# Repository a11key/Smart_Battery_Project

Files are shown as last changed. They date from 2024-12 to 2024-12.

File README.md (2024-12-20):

# Smart_Battery_Project
# Репозиторий проекта "УМНЫЙ АКБ для БАС"

## Министерство науки и высшего образования Российской Федерации  
### ФЕДЕРАЛЬНОЕ ГОСУДАРСТВЕННОЕ АВТОНОМНОЕ ОБРАЗОВАТЕЛЬНОЕ УЧРЕЖДЕНИЕ ВЫСШЕГО ОБРАЗОВАНИЯ  
### «МОСКОВСКИЙ ФИЗИКО-ТЕХНИЧЕСКИЙ ИНСТИТУТ (НАЦИОНАЛЬНЫЙ ИССЛЕДОВАТЕЛЬСКИЙ УНИВЕРСИТЕТ)» (МФТИ, Физтех)

---

## Описание проекта

**Название проекта:** УМНЫЙ АКБ для БАС

**Работу выполнили:**  
- Мацкевич Алексей
- Салахов Камиль 
- Васильев Андрей 

**Дата:** Долгопрудный, 19.12.2024

### Аннотация
Проект направлен на разработку аккумуляторного модуля для беспилотной авиационной системы (БАС), который позволяет передавать параметры АКБ (температуру, напряжение, ток заряда/разряда) на внешнее устройство.

### Цель и задачи
**Цель:** Создать модуль для БАС с возможностью беспроводной связи с внешним устройством для мониторинга параметров аккумуляторов в реальном времени.

**Задачи:**
1. Спроектировать корпус АКБ, позволяющий интегрировать плату для мониторинга параметров и передачи данных на внешнее устройство.
2. Спроектировать плату с датчиками для фиксации состояния АКБ.
3. Разработать программное обеспечение, которое сможет регистрировать данные в режиме реального времени или записывать их в память.

### Использованное оборудование
- 2 платформы Arduino Nano
- 2 высокоточных датчика температуры (±0,25 °C) MCP9808
- LM2596 DC-DC Module (встраиваемый стабилизатор напряжения)
- Датчик Холла ACS712
- 2 радиомодуля NRF24L01 PA LNA
- 3 резистора (10 кОм)

### Ход создания
1. Спроектирована схема основного и принимающего модулей.

2. Попытка распечатать плату под схему. Из-за неудачных попыток создания было принято решение спаять компоненты схемы проводами.

3. Проектирование соединения для соединения АКБ с модулем. Корпус из пластика, распечатанный на 3D-принтере, был бы громоздким и тяжелым, поэтому было принято решение скреплять плату более простым и эффективным способом.

4. Разработано приложение, отображающее параметры, которые были приняты с модуля, прикрепленного к АКБ.

5. Подобраны провода, которые пригодны для использования с аккумулятором Li-Po Fullymax 30C.

### Результаты работы
Создан модуль, позволяющий считывать температуру, напряжение и ток заряда/разряда с АКБ и передавать эти параметры на внешнее устройство.

---

## Установка и использование
В процессе...

---

Для получения дополнительной информации или вопросов, пожалуйста, свяжитесь с авторами проекта.

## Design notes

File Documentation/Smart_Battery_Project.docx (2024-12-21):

Министерство науки и высшего образования Российской Федерации

ФЕДЕРАЛЬНОЕ ГОСУДАРСТВЕННОЕ АВТОНОМНОЕ ОБРАЗОВАТЕЛЬНОЕ УЧРЕЖДЕНИЕ ВЫСШЕГО ОБРАЗОВАНИЯ «МОСКОВСКИЙ ФИЗИКО-ТЕХНИЧЕСКИЙ ИНСТИТУТ (НАЦИОНАЛЬНЫЙ ИССЛЕДОВАТЕЛЬСКИЙ УНИВЕРСИТЕТ)» (МФТИ, Физтех)

ПРОЕКТ

“Умная аккумуляторная батарея для беспилотного авиационного средства”

Работу выполнили: Мацкевич Алексей Б04-305

Салахов Камиль Б04-304

Васильев Андрей Б04-305

Долгопрудный, 2024

# Используемые обозначения

АКБ – аккумуляторная батарея;

БАС – беспилотное авиационное средство;

ПК – персональный компьютер;

ПО – программное обеспечение.

# Аннотация

В данной работе описано создание модуля, подключаемого к БАС (FlameWheel 450), для измерения параметров АКБ (Li-Po Fullymax 30C). Описанный модуль определяет напряжение, ток и температуру АКБ и отправляет эти данные на принимающее устройство (ПК).

Репозиторий с файлами проекта и его описанием: https://github.com/a11key/Smart_Battery_Project.

# Цель и задачи

Цели:

1. Создать модуль для БАС с возможностью беспроводной связи с внешним устройством для мониторинга параметров АКБ (напряжения, температуры, тока заряда/разряда) в реальном времени;
2. Создать ПО для визуализации полученных данных.

Задачи:

- Спроектировать корпус АКБ, позволяющий интегрировать в него плату для мониторинга параметров и передачи данных на внешнее устройство;
- Спроектировать устройство с антенной и датчиками для фиксации состояния АКБ;
- Разработать ПО, сохраняющие данные полученные с устройства, а также строящее графики зависимости фиксируемых величин в реальном времени.

# Требования к проекту

Устройство необходимо изготовить для считывания параметров батареи Li-Po Fullymax 30C (изображена на рисунке 1) при работе квадрокоптера FlameWheel 450 (изображен на рисунке 2).

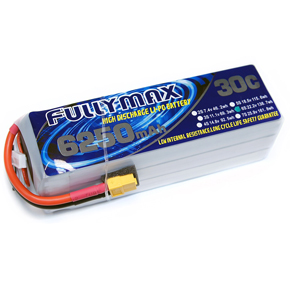
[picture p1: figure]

Рисунок 1 – Аккумулятор Li-Po Fullymax 30C

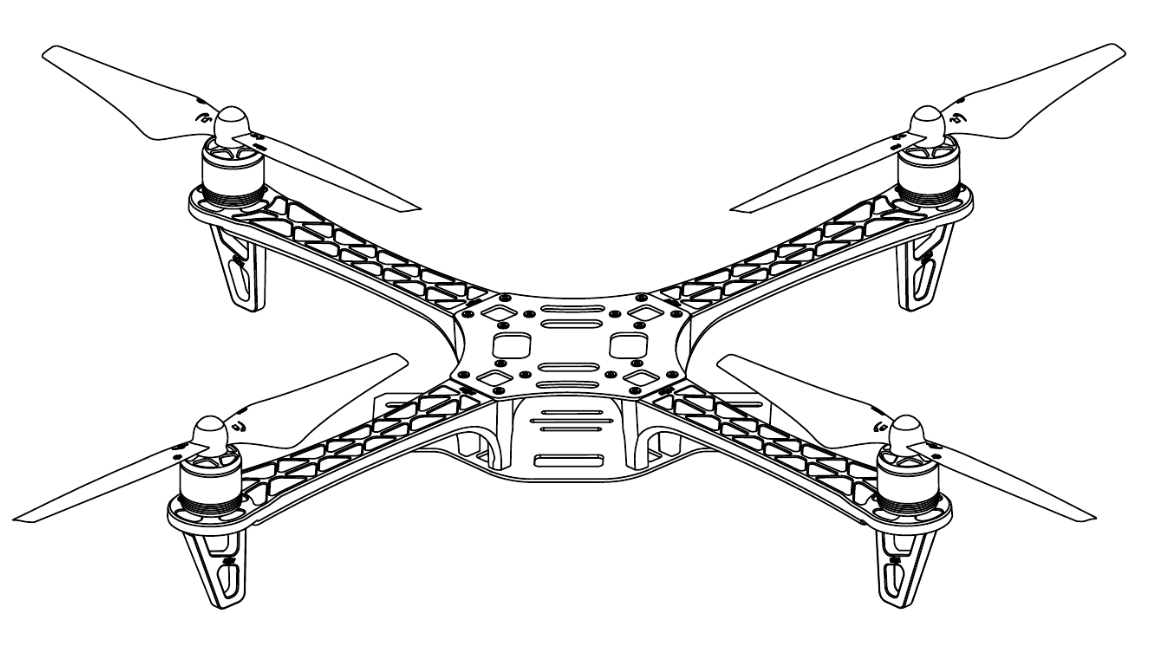
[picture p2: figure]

Рисунок 2 – Квадрокоптер FlameWheel 450

При работе над проектом были сформулированы следующие требования к устройству:

- Дальность действия более 100 м;
- Вес считывающего устройства менее 1/3 веса аккумулятора, то есть менее 130 г.;
- Максимальный потребляемый ток БАС: 30А, следовательно считывающее устройство должно выдерживать токи до 30А.

# Проектирование устройства

Считывающее устройство представляет собой перемычку, подключаемую между батареей и квадрокоптером, имеющую возможность считывать с батареи напряжение, ток и температуру и передавать данные на принимающее устройство.

Пронимающее устройство должно получать данные с считывающего устройства.

Для проектирования обоих устройств за основу был выбран микроконтроллер Arduino Nano.

## Измерение напряжения

Напряжение на аккумуляторе измеряется с помощью простого понижателя напряжения (рисунок 3).

Номиналы резисторов выбирались из следующих соображений:

- Так как аккумулятор получается замкнут на себя через понижающую схему, ток, проходящий через схему понижения, должен быть минимальным, то есть I_(load) ≫I_U . Максимальный ток можно оценить так: 20 А≫I_U . Таким образом суммарное сопротивление должно быть 1,7 Ом≪R_U (Минимальное напряжение аккумулятора ~ 12 В).
- Максимальное напряжение, которое может считать Arduino Nano: 5 В, значит, пониженное напряжение должно не превосходить этого значения.

В итоге были подобраны 3 резистора на 10 кОм. Коэффициент понижения – 3.

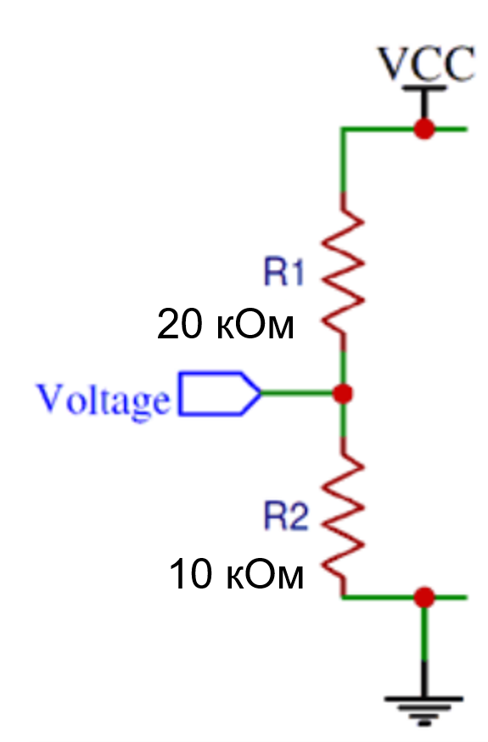
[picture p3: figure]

Рисунок 3 – Схема цепочки для понижения напряжения

## Измерение тока

Изначально планировалось измерять не ток, а напряжение на известном шунтирующем резисторе, а потом преобразовывать его с помощью операционного усилителя, как показано на рисунке 4. Но при подборе шунтирующего резистора оказалось, что резисторы имеющие достаточно маленькое сопротивление (менее 0,17 Ом) и выдерживают достаточно высокую мощность (порядка 300 Вт) имеют стоимость сопоставимую со стоимостью всех остальных компонентов устройства.

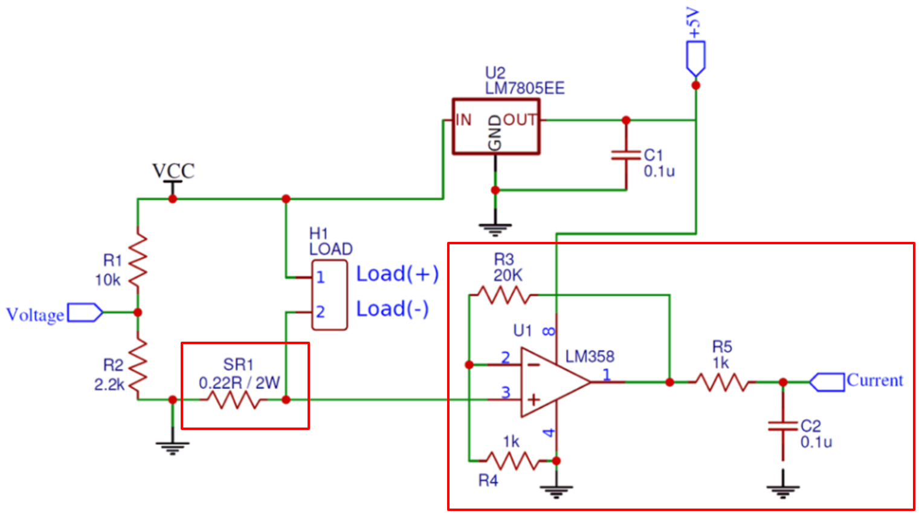
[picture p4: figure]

Рисунок 4 – Схема цепочки для понижения напряжения (часть схемы, используемая для определения силы тока, выделена красным)

Поэтому был выбран альтернативный вариант измерения тока: с помощью датчика ACS712 30A. Датчик рассчитан на максимальный пропускаемый ток 30А, что идеально подходит под требования, создаваемого устройства. Датчик ACS712 изображен на рисунке 5.

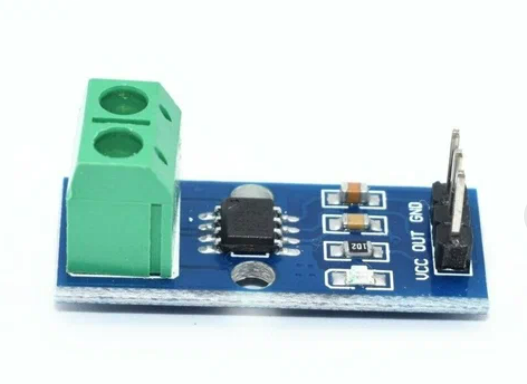
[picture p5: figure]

Рисунок 5 – Датчик тока ACS712 30A

## Измерение температуры

Для измерения температуры были выбраны высокоточные датчики MCP9808. Высокая точность датчиков температуры важна, так как при работе аккумулятора его температура повышается незначительно, однако определение зависимости различных других величин от температуры является ключевой задачей данного проекта. Датчик MCP9808 изображен на рисунке 6.

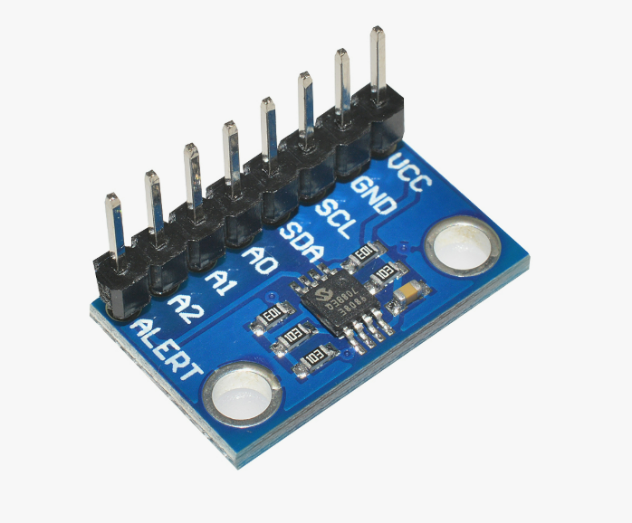
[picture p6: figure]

Рисунок 6 – Высокоточный датчик температуры MCP9808

В измеряющем устройстве было использовано 2 датчика температуры для усреднения температуры. Необходимость этого связана с неравномерностью нагрева АКБ.

## Передача и прием данных

Для передачи и приема данных были использованы радиомодули NRF24L01+PA+LNA, подключенные через специальный адаптер питания к микроконтроллеру. Внешний вид радиомодуля приведен на рисунке 7. Максимальное заявленное расстояние передачи данных – 1 км, что удовлетворяет требованиям к проекту.

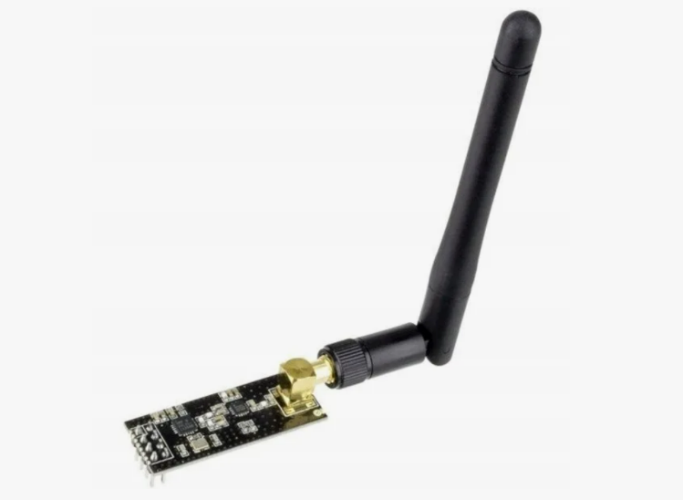
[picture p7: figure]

Рисунок 7 – Радиомодуль NRF24L01+PA+LNA

## Питание устройства

Измеряющее устройство питается с того же аккумулятора, характеристики которого она фиксирует. Питание происходит через стабилизатор LM2596 DC-DC Module, понижающий напряжение до 5 В. Стабилизатор LM2596 DC-DC Module изображен на рисунке 8.

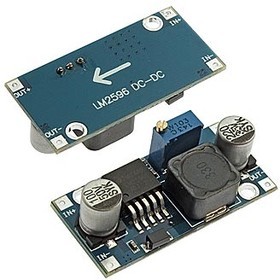
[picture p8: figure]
Фото 1/3 LM2596 DC-DC Module, Встраиваемый стабилизатор напряжения, Uвх=4-40VDC, Uвых=1.5-35VDC

Рисунок 8 – Стабилизатор LM2596 DC-DC Module

## Общая схема устройства

Общая схема измеряющего устройства приведена на рисунке 9.

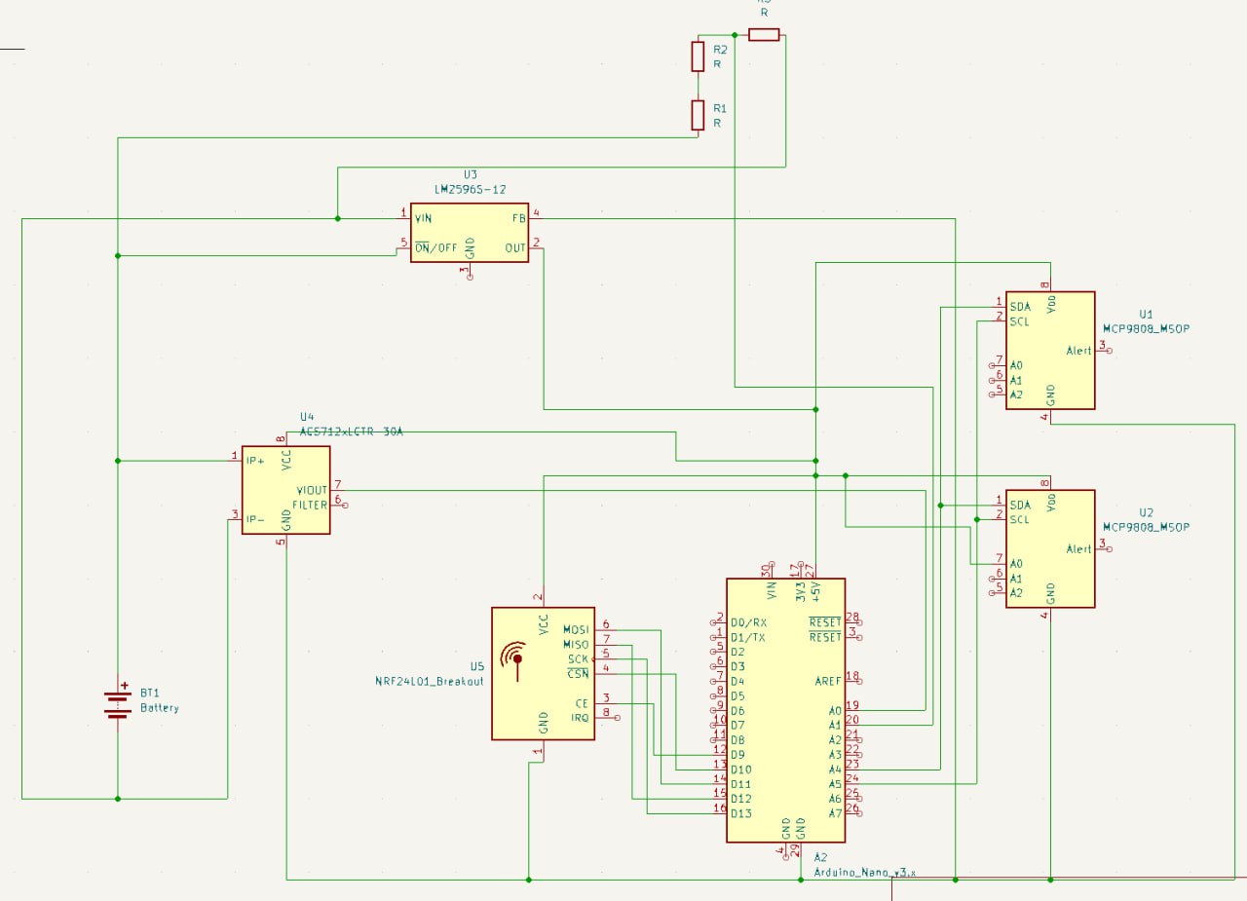
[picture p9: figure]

Рисунок 9 – Схема измеряющего устройства

Схема принимающего устройства изображена на рисунке 10.

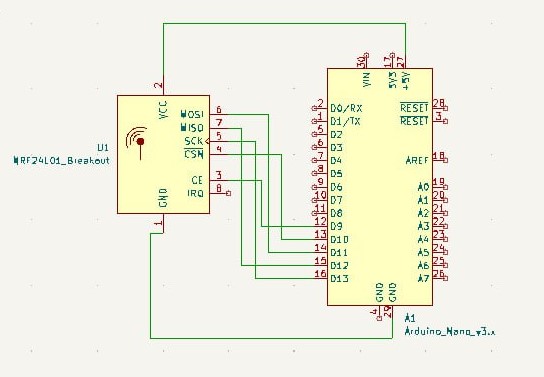
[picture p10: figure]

Рисунок 10 – Принимающего устройства

Изначально планировалось изготовить платы для обеих схем на фрезерно-гравировочном станке Charly 4U (изображен на рисунке 11). Однако после двух неудачных попыток изготовления было решено собирать устройства на макетной плате.

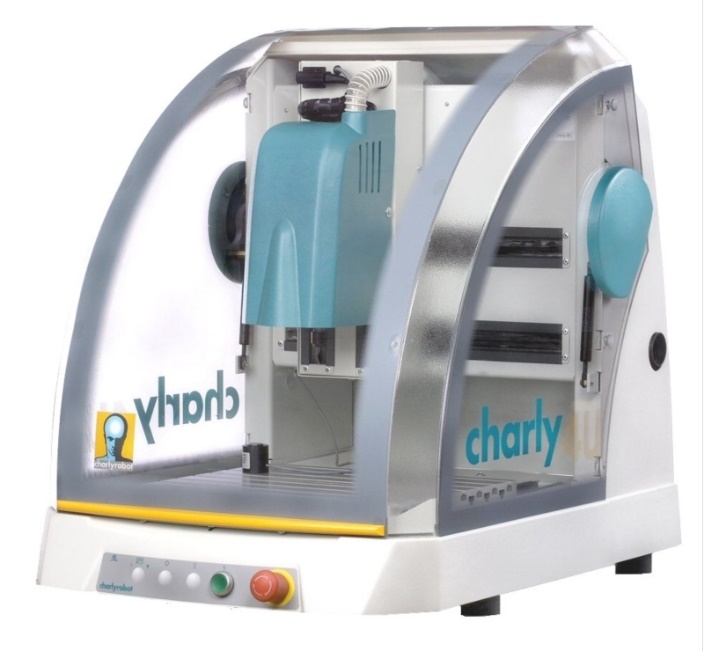
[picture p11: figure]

Рисунок 11 – Фрезерно-гравировочный станок Charly 4U

Разведенная плата принимающего устройства, которую пытались изготовить изображена на рисунке 12.

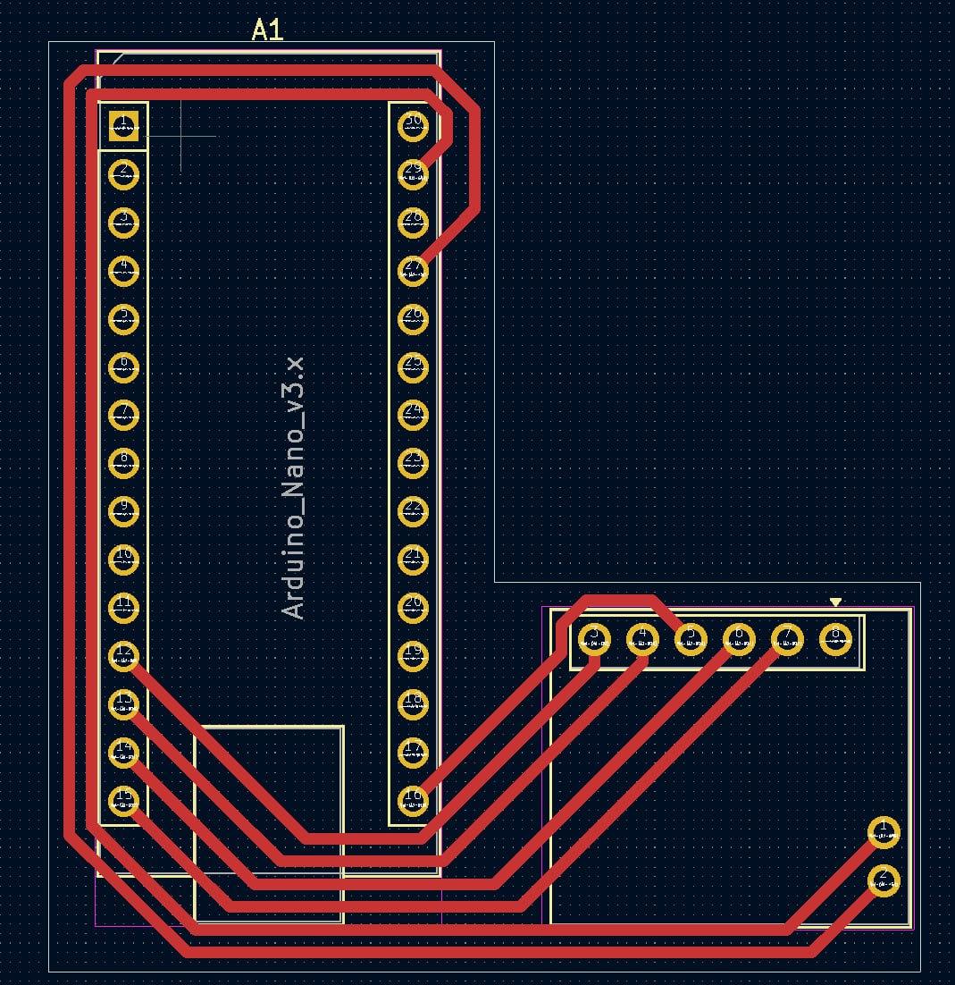
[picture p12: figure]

Рисунок 12 – Схема принимающего устройства

Фото изготовленных устройств представлено на рисунке 13.

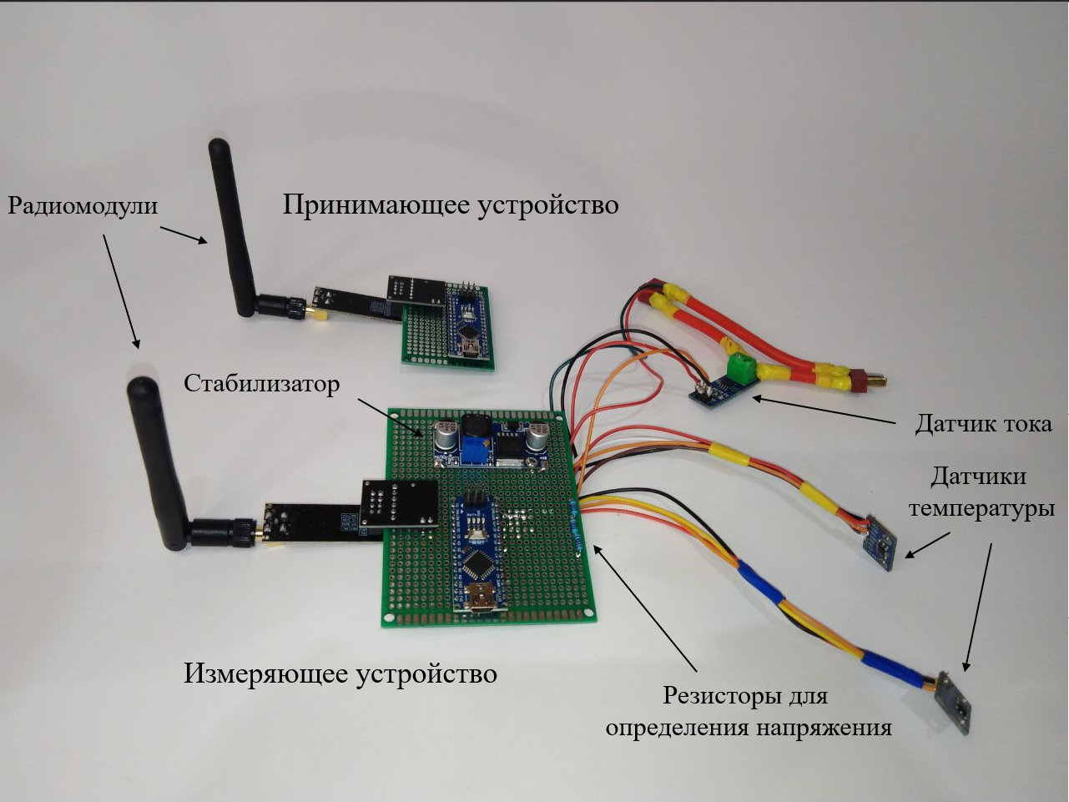
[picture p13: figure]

Рисунок 13 – Готовые измеряющее и принимающие устройства

# Интерфейс

Для визуализации снятых данных было разработано ПО на python. Был сделан следующий функционал:

- Выведение текущих значений характеристик аккумулятора;
- Построение графиков зависимостей измеряемых величин от времени в реальном времени.

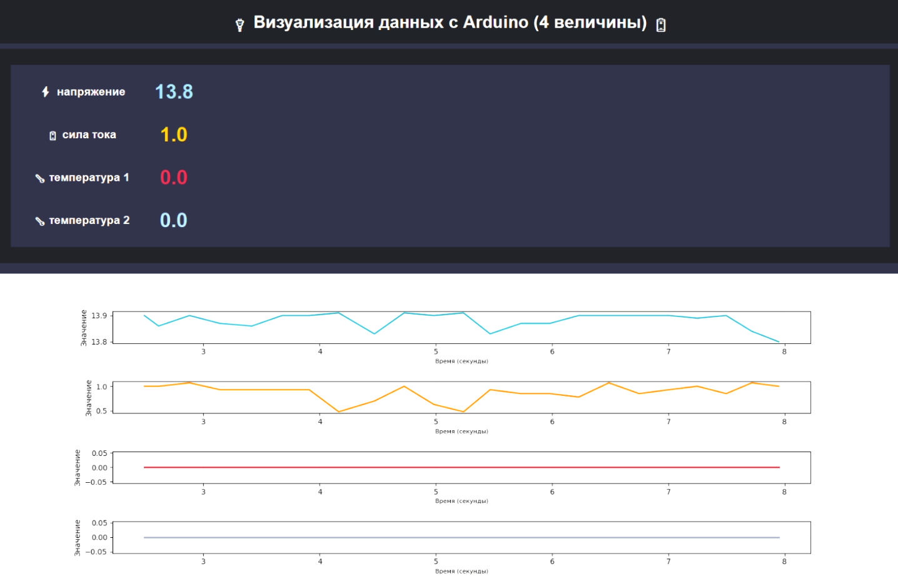
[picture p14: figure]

Рисунок 14 – Интерфейс для вывода снятых данных

# Проектирование креплений и корпуса

## Крепление АКБ и измерительной платы на БАС

Изначально планировалось изготовить специальное крепление на БАС для АКБ с измеряющим устройством. Вариант модели крепления представлен на рисунке 15.

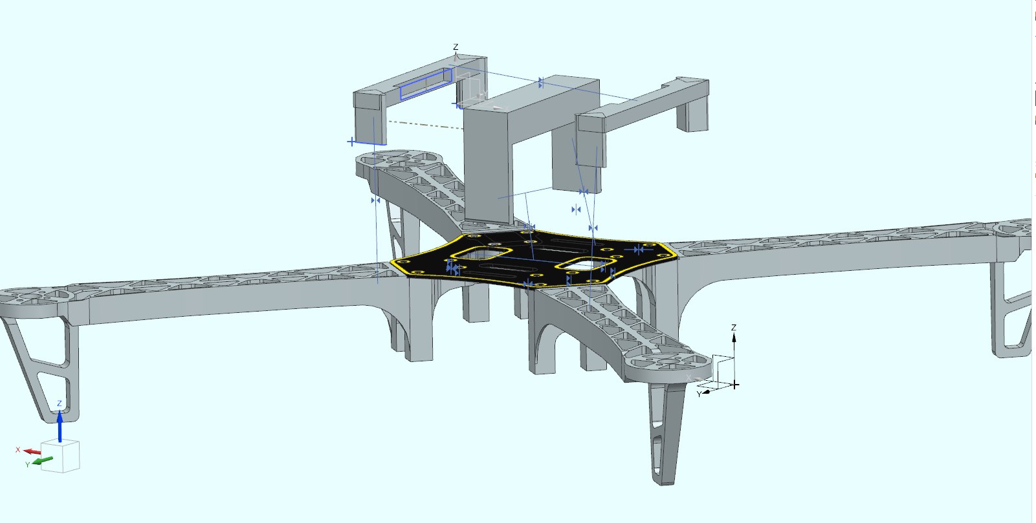
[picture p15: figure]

Рисунок 15 – Вариант крепления АКБ и измерительной платы к БАС

Однако позже было решено отказаться от данной модели. Корпус из пластика, распечатанный на 3D принтере, был бы громоздким, тяжелым, поэтому было принято решение скреплять плату более простым и эффективным способом.

## Корпус для принимающего устройства

Была попытка изготовления корпуса для принимающего устройства, однако из-за неудачного проектирования модели изготовить функциональный корпус не удалось. Модель корпуса и принимающее устройство изображены на рисунке 16.

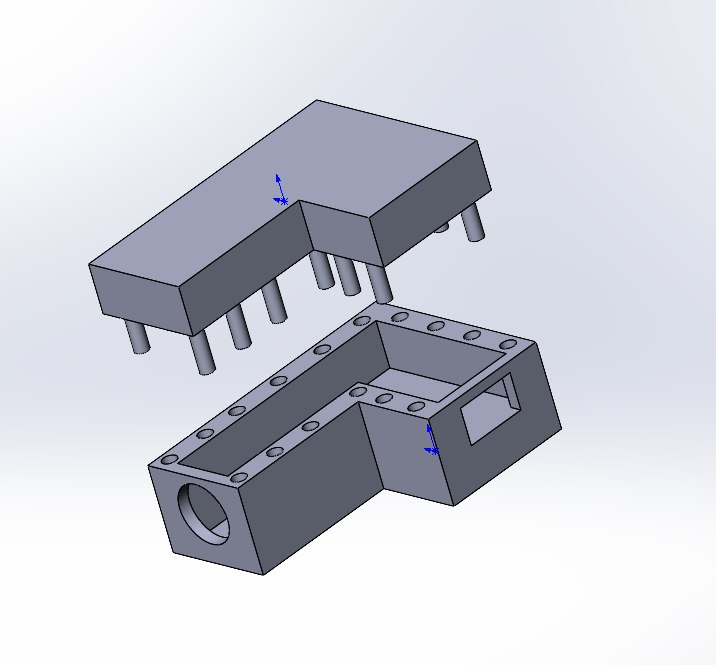
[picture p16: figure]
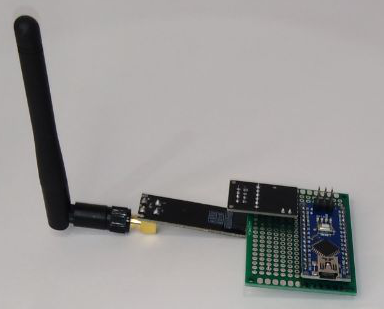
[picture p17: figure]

Рисунок 16 – Корпус для принимающего устройства и само устройство

# Результаты

1. Создан модуль, позволяющий считывать температуру, напряжение, ток заряда/разряда с АКБ и передавать эти параметры на внешнее устройство.
2. Разработано ПО для визуализации считанных данных.

На рисунке 17 изображено изготовленное устройство, присоединенное к АКБ и БАС.

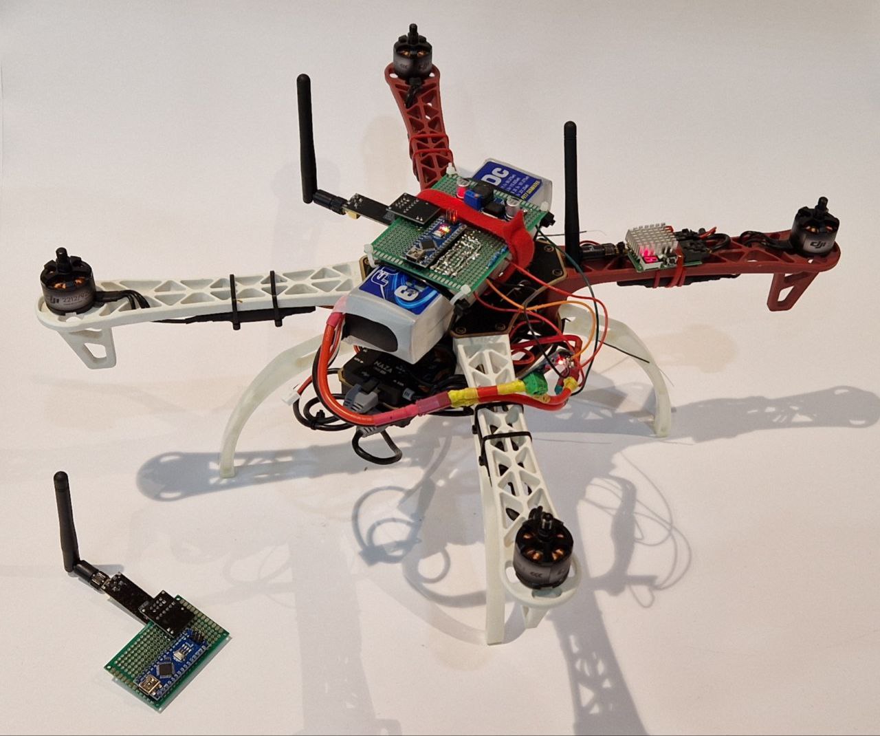
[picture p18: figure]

Репозиторий с файлами проекта и его описанием: https://github.com/a11key/Smart_Battery_Project.

# Дальнейшее развитие проекта

Планы по дальнейшему развитию проекта:

- Изготовить плату для считывающего и принимающего устройства;
- Сделать корпус для принимающего модуля;
- Спроектировать надежное и легкое крепление модуля с АКБ;
- Доработать ПО.

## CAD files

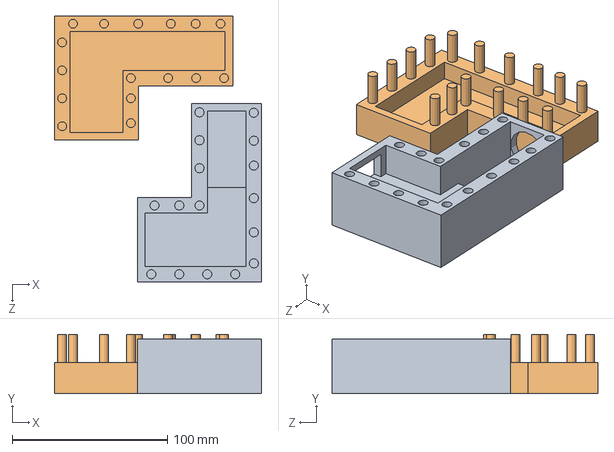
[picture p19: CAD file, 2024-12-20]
body_model/Сборка2.SLDASM
133.5 x 38.0 x 171.3 mm
корпус1
корпус2

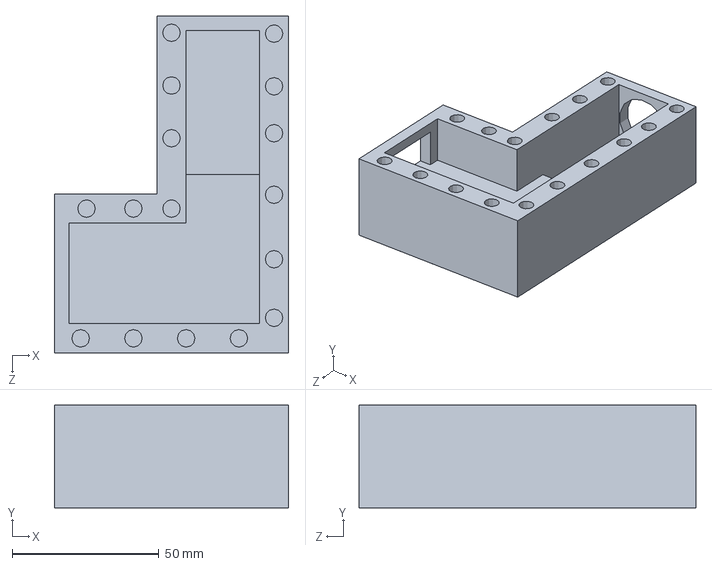
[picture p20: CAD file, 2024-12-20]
body_model/корпус1.SLDPRT
80.0 x 35.0 x 115.0 mm

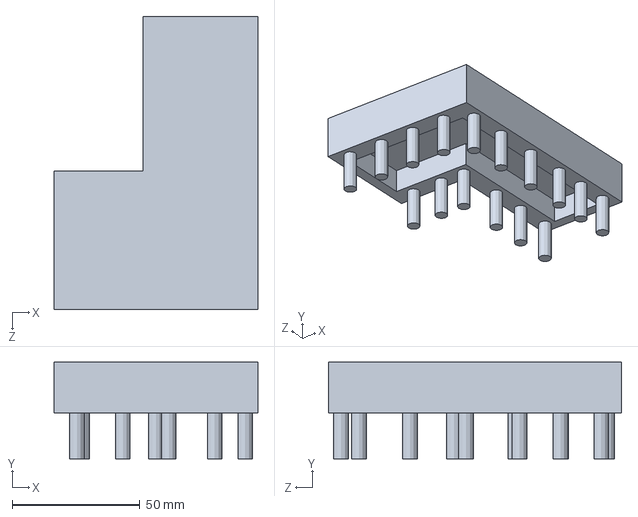
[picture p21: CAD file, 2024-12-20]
body_model/корпус2.SLDPRT
80.0 x 38.0 x 115.0 mm

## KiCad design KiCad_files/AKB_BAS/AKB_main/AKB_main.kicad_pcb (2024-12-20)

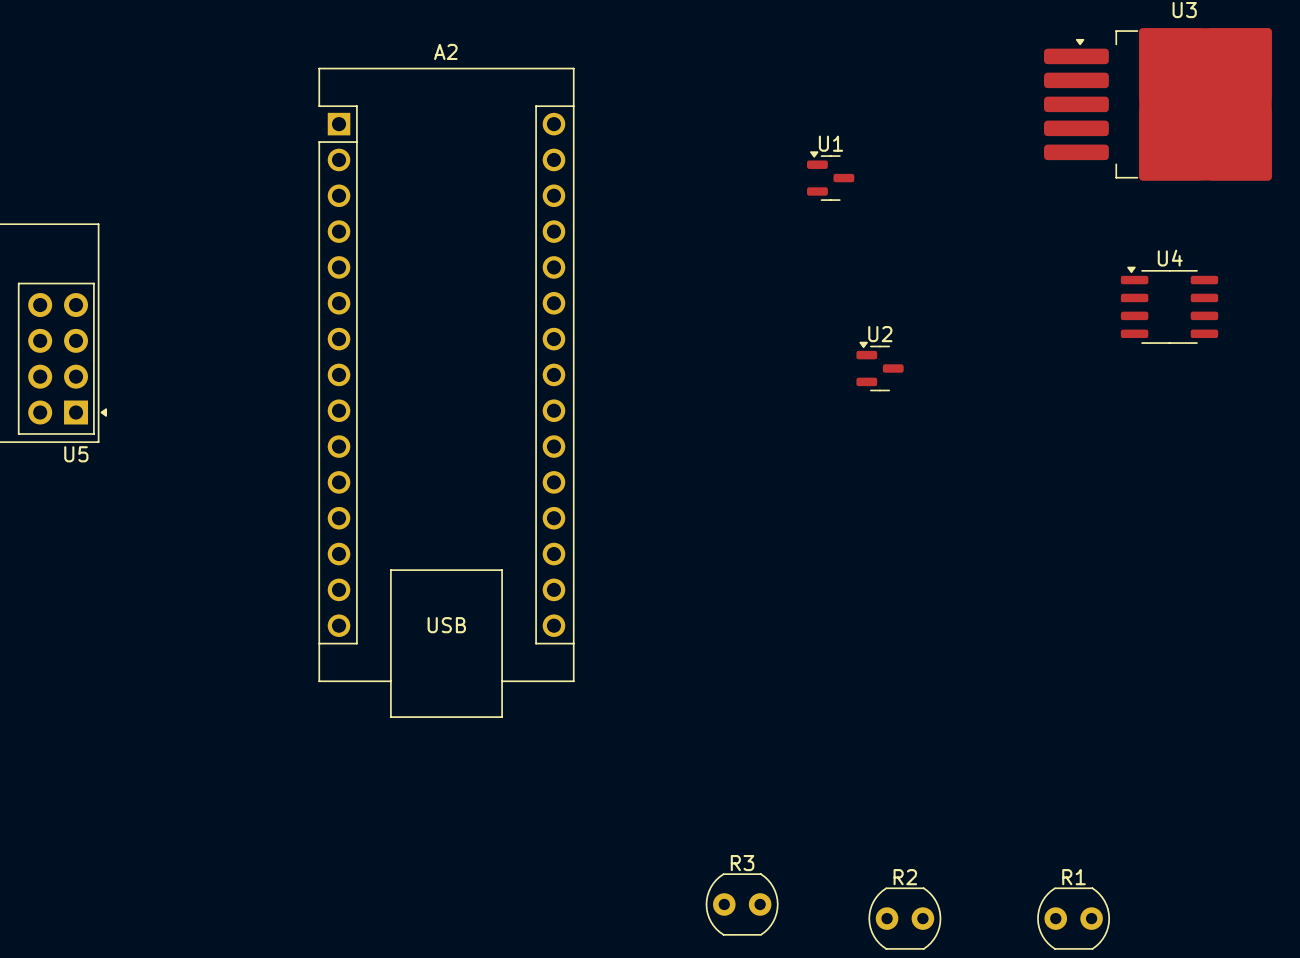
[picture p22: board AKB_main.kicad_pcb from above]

Board: 2 copper layers, 9 parts (0 on the bottom side), 9 nets, no tracks yet.

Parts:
A2: Arduino_Nano_v3.x; Arduino_Nano
R1, R2, R3: R; R_LDR_4.9x4.2mm_P2.54mm_Vertical
U1, U2: MCP9808_MSOP; SOT-23
U3: LM2596S-12; TO-263-5_TabPin3
U4: ACS712xLCTR-30A; SOIC-8_3.9x4.9mm_P1.27mm
U5: NRF24L01_Breakout; nRF24L01_Breakout

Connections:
unnamed: A2.27 (+5V), U5.2 (VCC)
unnamed: A2.12 (D9), U5.3 (CE)
unnamed: A2.13 (D10), U5.4 (~CSN)
unnamed: A2.14 (D11), U5.6 (MOSI)
unnamed: A2.15 (D12), U5.7 (MISO)
unnamed: A2.16 (D13), U5.5 (SCK)
unnamed: U4.1 (IP+), U4.2 (IP+)
unnamed: U4.3 (IP-), U4.4 (IP-)
unnamed: A2.29 (GND), U5.1 (GND)

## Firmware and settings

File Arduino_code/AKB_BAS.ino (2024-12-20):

// NRF24L01+ PA/LNA https://microkontroller.ru/arduino-projects/kak-rabotaet-modul-nrf24l01-i-kak-ego-podklyuchit-k-arduino/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
#include <SPI.h>                                          // Подключаем библиотеку для работы с шиной SPI
#include <nRF24L01.h>                                     // Подключаем файл настроек из библиотеки RF24
#include <RF24.h>                                         // Подключаем библиотеку для работы с nRF24L01+

RF24           radio(9, 10);                              // Создаём объект radio для работы с библиотекой RF24, указывая номера выводов nRF24L01+ (CE, CSN) 

//T
#include <Wire.h>
#include "Adafruit_MCP9808.h"

// Create the MCP9808 temperature sensor objects
Adafruit_MCP9808 tempsensor = Adafruit_MCP9808();
Adafruit_MCP9808 tempsensor_2 = Adafruit_MCP9808();

const int V_Pin = A1;     // voltage pin
double V = 0; // voltage value

const int currentPin = A0; // current pin
double I = 0; // current value
double sensitivity = 66 / 1000; // for 30 A


double data[4];

void setup() {
  Serial.begin(9600);  

  // NRF24L01+ PA/LNA
  radio.begin();                                        // Инициируем работу nRF24L01+
    radio.setChannel(126);                                  // Указываем канал передачи данных (от 0 до 127), 5 - значит передача данных осуществляется на частоте 2,405 ГГц (на одном канале может быть только 1 приёмник и до 6 передатчиков)
    radio.setDataRate     (RF24_250KBPS);                   // Указываем скорость передачи данных (RF24_250KBPS, RF24_1MBPS, RF24_2MBPS), RF24_1MBPS - 1Мбит/сек
    radio.setPALevel      (RF24_PA_MAX);                 // Указываем мощность передатчика (RF24_PA_MIN=-18dBm, RF24_PA_LOW=-12dBm, RF24_PA_HIGH=-6dBm, RF24_PA_MAX=0dBm)
    radio.openWritingPipe (0x1234567890LL);               // Открываем трубу с идентификатором 0x1234567890 для передачи данных (на одном канале может быть открыто до 6 разных труб, которые должны отличаться только последним байтом идентификатора)
    pinMode(2, INPUT);
                                

  // T
   if (!tempsensor.begin(0x18)) {
  Serial.println("Couldn't find MCP9808! Check your connections and verify the address is correct. 1");
  while (1);
  }
  if (!tempsensor_2.begin(0x19)) {
  Serial.println("Couldn't find MCP9808! Check your connections and verify the address is correct. 2");
  while (1);
  }
    
   Serial.println("Found MCP9808!");

  tempsensor.setResolution(3);
  tempsensor_2.setResolution(3); // sets the resolution mode of reading, the modes are defined in the table bellow:
  // Mode Resolution SampleTime
  //  0    0.5°C       30 ms
  //  1    0.25°C      65 ms
  //  2    0.125°C     130 ms
  //  3    0.0625°C    250 ms



}

void loop() {
  tempsensor.wake();   // wake up, ready to read!
  tempsensor_2.wake(); 

  // Read and print out the temperature, also shows the resolution mode used for reading.
  // Serial.print("Resolution in mode: ");
  // Serial.println (tempsensor.getResolution());
  double T1 = tempsensor.readTempC();

  //   Serial.print("2 Resolution in mode: ");
  // Serial.println (tempsensor_2.getResolution());
  double T2 = tempsensor_2.readTempC(); 
  
  delay(20);
  tempsensor.shutdown_wake(1); // shutdown MSP9808 - power consumption ~0.1 mikro Ampere, stops temperature sampling
  tempsensor_2.shutdown_wake(1);
  delay(20);

  V = analogRead(V_Pin)* (5.0 / 1023.0)*3.0;     // read voltage 

  I = analogRead(currentPin) * (5.0 / 1023.0)/sensitivity;

  data[0] = T1;
  data[1] = T2;
  data[2] = V;
  data[3] = I;

  for (int i = 0; i < 4; i ++) Serial.println(data[i]);

  // antenna
  radio.write(&data ,sizeof(data));
  delay(10);
}

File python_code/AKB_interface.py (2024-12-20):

import tkinter as tk
from tkinter import ttk
import serial
import threading
import time
import csv
from matplotlib.figure import Figure
from matplotlib.backends.backend_tkagg import FigureCanvasTkAgg

# Настройки последовательного порта
SERIAL_PORT = 'COM5'  # Замените на ваш порт
BAUD_RATE = 9600

# Параметры графика
MAX_POINTS = 50

# Функция проверки чисел с плавающей точкой
def is_float(value):
    try:
        float(value)
        return True
    except ValueError:
        return False

# Функция обновления графиков
def update_graphs():
    for time_data, sensor_data, line, ax in zip(
            [time_points, time_points, time_points, time_points],
            [sensor_values1, sensor_values2, sensor_values3, sensor_values4],
            [line1, line2, line3, line4],
            [ax1, ax2, ax3, ax4]):
        if len(time_data) > MAX_POINTS:
            time_data.pop(0)
            sensor_data.pop(0)

        line.set_data(time_data, sensor_data)
        ax.relim()
        ax.autoscale_view()

    canvas.draw()  # Прямое обновление холста

# Функция автоматического обновления графиков
def auto_update_graphs():
    update_graphs()
    root.after(100, auto_update_graphs)

# Функция для чтения данных с Arduino
def read_from_arduino():
    try:
        with open("arduino_data.csv", "w", newline="") as csvfile:
            csvwriter = csv.writer(csvfile)
            csvwriter.writerow(["Время", "Значение 1", "Значение 2", "Значение 3", "Значение 4"])

            while True:
                try:
                    # Чтение строки из порта
                    data = ser.readline().decode('utf-8').strip()
                    print(f"Полученные данные: {data}")  # Отладочное сообщение

                    # Разделение строки на значения
                    values = data.split()

                    # Проверка на корректность формата (должно быть 4 значения с плавающей точкой)
                    if len(values) == 4 and all(is_float(v) for v in values):
                        value1, value2, value3, value4 = map(float, values)
                        current_time = time.time() - start_time

                        # Обновление данных для графиков
                        time_points.append(current_time)
                        sensor_values1.append(value1)
                        sensor_values2.append(value2)
                        sensor_values3.append(value3)
                        sensor_values4.append(value4)

                        # Запись в CSV
                        csvwriter.writerow([current_time, value1, value2, value3, value4])

                        # Обновление значений в Tkinter
                        sensor_value1.set(value1)
                        sensor_value2.set(value2)
                        sensor_value3.set(value3)
                        sensor_value4.set(value4)
                    else:
                        print(f"Неверный формат данных: {data}")  # Отладка
                except Exception as e:
                    print(f"Ошибка при обработке данных: {e}")  # Лог ошибки
                time.sleep(0.1)
    except Exception as e:
        print(f"Ошибка при открытии файла или порта: {e}")

# Функция закрытия приложения
def close_app():
    ser.close()
    root.quit()

# Создаем окно Tkinter
root = tk.Tk()
root.title("Визуализация данных с Arduino (4 величины)")
root.geometry("900x1100")
root.config(bg="#2B2D42")

# Заголовок
title_label = tk.Label(root, text="🔌 Визуализация данных с Arduino (4 величины) 🔋", 
                       font=("Helvetica", 24, "bold"), fg="#FFFFFF", bg="#1B1E23", pady=20)
title_label.pack(fill=tk.X)

# Отображение текущих значений
sensor_value1 = tk.DoubleVar()
sensor_value2 = tk.DoubleVar()
sensor_value3 = tk.DoubleVar()
sensor_value4 = tk.DoubleVar()
sensor_value1.set(0)
sensor_value2.set(0)
sensor_value3.set(0)
sensor_value4.set(0)

value_frame = tk.Frame(root, bg="#1B1E23", pady=20, padx=10)
value_frame.pack(fill=tk.X, pady=(10, 20))

# Добавление рамки
value_inner_frame = tk.Frame(value_frame, bg="#2B2D42", pady=10, padx=20)
value_inner_frame.pack(pady=10, padx=10, fill=tk.X)

for i, (var, label_text, color) in enumerate(
    zip([sensor_value1, sensor_value2, sensor_value3, sensor_value4],
        ["⚡ напряжение", "🔋 сила тока", "🌡 температура 1", "🌡 температура 2"],
        ["#8ECAE6", "#FFB703", "#E63946", "#A2D2FF"])):
    tk.Label(value_inner_frame, text=label_text, font=("Helvetica", 16, "bold"), 
             fg="#FFFFFF", bg="#2B2D42").grid(row=i, column=0, padx=20, pady=15)
    lbl = tk.Label(value_inner_frame, textvariable=var, font=("Helvetica", 28, "bold"), 
                   fg=color, bg="#2B2D42")
    lbl.grid(row=i, column=1, padx=20, pady=15)

# Настройка графиков
fig = Figure(figsize=(8, 10), dpi=100, tight_layout=True)
gs = fig.add_gridspec(4, 1, hspace=1.2)

ax1 = fig.add_subplot(gs[0, 0])
ax2 = fig.add_subplot(gs[1, 0])
ax3 = fig.add_subplot(gs[2, 0])
ax4 = fig.add_subplot(gs[3, 0])

for ax in [ax1, ax2, ax3, ax4]:
    ax.set_xlabel("Время (секунды)", fontsize=8)
    ax.set_ylabel("Значение", fontsize=10)
    ax.grid(color="#CCCCCC", linestyle="--", linewidth=0.5)

line1, = ax1.plot([], [], color='#219EBC', linewidth=2)
line2, = ax2.plot([], [], color='#FB8500', linewidth=2)
line3, = ax3.plot([], [], color='#D62828', linewidth=2)
line4, = ax4.plot([], [], color='#8D99AE', linewidth=2)

canvas = FigureCanvasTkAgg(fig, master=root)
canvas.get_tk_widget().pack(fill=tk.BOTH, expand=True)

# Подготовка для чтения данных
ser = serial.Serial(SERIAL_PORT, BAUD_RATE, timeout=1)
time_points = []
sensor_values1 = []
sensor_values2 = []
sensor_values3 = []
sensor_values4 = []
start_time = time.time()

# Поток для чтения данных
read_thread = threading.Thread(target=read_from_arduino, daemon=True)
read_thread.start()

# Запуск автообновления графиков
auto_update_graphs()

# Запуск основного цикла Tkinter
root.protocol("WM_DELETE_WINDOW", close_app)
root.mainloop()

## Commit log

2024-12-18 Added operating code AKB_BAS.ino (with out antenna)
2024-12-20 added all files
    [AKB_BAS-B_Cu.gbr, AKB_BAS-B_Mask.gbr, AKB_BAS-B_Paste.gbr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]
